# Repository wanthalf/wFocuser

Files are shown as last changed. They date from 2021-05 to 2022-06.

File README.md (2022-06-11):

# wFocuser (extension of myFocuserPRO2 ESP)

This is my private extension of the original "myFP2ESP Firmware for ESP32 and ESP8266 myFP2ESP Controllers" by Robert Brown, Holger Manz and Paul Porters, forked from the [brownrb/myFP2ESPFirmware](https://github.com/brownrb/myFP2ESPFirmware) repository. The original README.md is renamed to [README.myFP2ESP.md](README.myFP2ESP.md) and contains links to the original project information and documentation.

## Motivation and changes

MyFocuser is a marvellous project (actually a group of projects) for building DIY electronic focusers primarily aimed at astrophotography. They cover various combinations of hardware components suitable for differently sized equipment (telescopes or photolenses). However, the broad field of supported components and their features has its limits, of course. Once you get used to the peculiarities of this project and occasional inconsistencies or contradictions within the otherwise admirable, long and detailed documentation, you may want to adapt or extend the focuser to your own needs or ideas. My desire was to get beyond two basic limitations of the original project based on the ESP32 microcontroller:
1. MyFocuser is primarily aimed at *remote control*, but it already implements two pushbuttons for local quick adjustment of the focus and an OLED display for information about the focuser. I wanted to be able to use the pushbuttons to control all the main functions of the focuser *locally*, too. For that purpose I added two more pushbuttons and extended the source code of the firmware to fully utilize the possibilities of the OLED display.
2. The original documentation expects you to use one of the pre-designed PCB boards. That seems rather a complication to me (where to get it?) and it also expects you to place the focuser board into a relatively large box and use robust cable interconnections with other components (stepper motor, sensors etc.); I wanted a more compact and lightweight build suitable for travelling with my portable equipment (ExploreScientific iExos-100 mount controlled by a small Astroberry) which could ideally be fixed directly to the telescope tube.

My build is based on the ESP32 controller, SH1106 OLED 1,3" display, TMC2209 driver and a NEMA17-PG27 motor. I tried to modify the firmware with the effort of the minimal possible interventions in order to keep backward compatibility with all the originally supported hardware components and features, but I cannot guarantee I did not really break anything. I cannot test or "support" any other hardware combinations (beyond theoretical help), but I tried to avoid disrupting any of the functionality of the original firmware.

The changes concern:

- the original pushbuttons (called UP/DOWN) have their primary functionality modified so that they can move the focuser in smaller or larger (but exact) amount of steps, depending on the length of their press
- adding two more push buttons called MOD(ifier) and SET to control all functions of the focuser locally via an interactive menu; use of an OLED display is needed

## Advanced control in detail

The display can show 4 different basic screens (pages) which can be switched by a short press of the SET button:

1. MAIN page is almost identical with the original screen in OLED_GRAPHIC mode: it shows the focuser's current position, direction of movement and target position, as well as the maximal position, step size, backlash, temperature (if available), "heart beat" symbol and an additional symbol to indicate connection of remote client; only this page allows the UP/DOWN buttons to be used to move the focuser interactively\
MAIN PAGE
2. PRESET page allows to apply one of the 10 available presets or to edit/change their values\
PRESETS PAGE
3. SETTINGS page allows to change the following 10 most important settings: enable or disable home position switch, temperature probe, backlash-in and backlash-out compensation; changing the value of the current and maximal position (without moving the focuser); changing motor speed, step size, backlash-in and backlash-out amount of steps\
SETTINGS PAGE
4. NETWORK information: showing the current SSID and IP address of the WiFi connection and state of the remote client connection (ASCOM/INDI)

### Turning the display ON/OFF

The original behaviour of myFocuser is kept: when the firmware stores the changed position or settings into permanent memory, the display turns off automatically; this usually happens 30 seconds after the last movement or change of any setting. However, manual control can also be used:

- pressing any button (also just the MOD button) turns the display on
- long press of the SET button turns the display off

This behaviour is available independently of the screen/page shown.

### MAIN page

- UP/DOWN buttons can be directly used to move the focuser: a short press moves it immediately by a single step, if the button remains pressed for at least 200ms, it adds 9 more steps to reach the sum of 10, and a very long press (>900ms) adds another 90 steps to reach a full movement of 100 steps; this functionality is not dependent on the availability of a display and can be disabled by commenting out the line `#define ADVANCED_PB_MOVEMENT` in `focuserconfig.h` (then the buttons will behave as in the original firmware); at the same place in the configuration, you can also modify the press length times/thresholds for the short/bold and long press (`BOLDPRESS`, `LONGPRESS`) and the step sizes for each movement phase (`SHORT_STEPS`, `BOLD_STEPS`, `LONG_STEPS`)
- MOD + UP/DOWN: changes the numeric value of the target position shown on the display (the longer you press the buttons, the faster the numbers change); unlike the direct movements, where the UP button moves the focuser inwards (towards position 0) and the DOWN button outwards (towards maximal position), here the UP button changes the value up towards the maximal position and the DOWN button down to zero
- MOD + SET: move the focuser to the target position set by pressing MOD + UP/DOWN; a confirmation screen will appear (press UP to confirm or DOWN to cancel the movement)
- MOD + SET (long press): move the focuser to home position 0 (confirmation will be required too)

### PRESET page

- UP/DOWN: move between the 10 presets; if some preset value is already changed, a confirmation will be required to store or cancel the new value before moving to another preset
- MOD + UP/DOWN: change the value of the current preset; a changed value is indicated by the cursor changing into a rectangle (losing its inversion)
- MOD + SET: move the focuser to the currently selected preset position; confirmation will be required; if the preset value has been changed, another confirmation to store the value will be required first
- MOD + SET (long press): current focuser position will be set as the new value for the selected preset
- SET: switching to next page will cancel any change to the value of the current preset

### SETTINGS page

- UP/DOWN: move between the 10 available settings
- MOD + UP/DOWN: changes the current setting value; on/off values are changed immediately, numeric values are changed like the presets and need to be confirmed in order to be stored permanently (after moving UP/DOWN, away from the current setting)

## Hardware changes

After some experiments, I found out the 28BYJ-48 won't be capable to reliably move the focuser of my telescope. Therefore I deployed the "large and heavy" NEMA17-PG27 which also has very fine steps without the need for microstepping.

I managed to fit the whole controller (including the 4 push buttons) onto a small 40x60mm PCB breadboard as documented in detail in the [hardware](hardware/) folder. Together with the motor and the 1,3" OLED display, it fits comfortably into a box the size of 112x75x58mm. Of course, my build is not as robust and "clean" as the original projects based on a proper PCB and quality wiring.

The two additional pushbuttons (=the GPIO pins they are connected to) must be configured in the board configuration JSON file uploaded to the board. I modified only the `data/boards/57.jsn` configuration for the TM2209 drivers. If you use a different driver, you have to add the two additional GPIO pin assignments to the corresponding configuration file.

By accident, I also connected the second button (DOWN) to GPIO 25 instead of the original GPIO 35. But you can just revert that setting in `data/boards/57.jsn` and use the original pin.

## TMC2209 and StallGuard (remaining problems)

I did not manage to make the StallGuard work with the NEMA17-PG27 motor. The StallGuard alert is triggered by the TM2209 at nearly every start and stop of the motor movement (especially when several short moves follow each other), whatever value of the SG threshold I tried. For now, I have attached an infrared sensor to detect the home position, but a mechanical switch would probably be more precise. I still wonder whether accelerated driver control (such as AccelStepper or FastAccelStepper) would possibly help as suggested in some discussions about this kind of problems with TMC2209.

I also didn't find any real effect of all the TM2209 calculations and settings suggested in the documentation. The most important one of them (the CS value) is not set anywhere in the original firmware code anymore. I didn't observe any significant change when playing with the values, nor any significantly helpful effect on the false StallGuard alerts. But I am no expert in motor control, so I would be very thankful for any better explanation.

I also did not find the default microstepping of 4 helpful in combination with the PG27 gear of the motor and set it back to 1. Also the motor speed delay of at least 2000 seems more appropriate for the motor. Those are the other changes in the default TM2209 configuration in `data/boards/57.jsn`.

## Other questions I did not find an answer to in the official documentation

(Maybe just because I did not read everything thoroughly enough?)

#### What is the exact original behaviour of the pushbuttons?

As stated in the documentation, the pushbuttons are (originally) suitable for finer adjustments of the focuser, but not for significant movements. In practice, the pushbuttons move the focuser by a single step as long as they are pressed. That means: by one step each time the button is tested for press. The buttons are not tested when the focuser is moving. But single step movements are very short, so that you always get a movement of several steps at once even if you press the button just shortly. If you keep it pressed, the movements start to add in short intervals, so that you can reach a change of position of several dozens steps in reasonable time. In this way, you can realistically move the focuser by about 100 steps or even more with a bit of patience, but larger movements would just take too much time (several minutes).

#### Do I need to buy components from the suggested sellers?

Of course not. But if you want to use the pre-designed PCBs, you have to watch out that you buy an identical version with the same dimensions and pinout. The ESP32 modules are produced in various versions. They may have a different number of pins even though they look similar. Basically, the ESP32 modules with a single row of pins on each side are produced with 2x15 pins or 2x19 pins - the first one is the one you want for this project.

You need to take care especially in the case of the TMC2209 modules. The version from BigTreeTech is probably really unavoidabe, because other modules have not only a different pinout, but they may even be missing some important pins completely.

#### Do I need to use the pre-designed PCB?

No. But the whole documentations expects you to do it. The original PCB designs support all the available options and you may freely switch between them. That is not necessarily what you plan to do. However, you may change your mind when you try working with the focuser, so this gives you some flexibility. The original PCB gives you a lot of flexibility and robustness, but it also takes some space.

The whole wiring is actually not as complicated as it may seem at the first look. The most "complicated" is the power circuit. It contains a voltage regulator to reduce the 12V power to the 8V or 5V needed by the microcontroller, three or four capacitors, a diode and a fuse. All the rest are just interconnections between the ESP32 and its peripherals (with occasional pull-up or pull-down resistors): the stepper driver, OLED display, joystick or push buttons, temperature probe and IR sensor. The default wiring scheme also includes additional jumper headers to allow you to switch between the exclusive options in case you change your mind. These make the wiring seem more complex than it is.

#### What are all the options available?

It may be a bit difficult to find your way among all the options and variants of myFocuser at first. A great deal of information is spread to several places in the documentation and while there may be occasional inconsistencies or even contradictions between them, it is worth to find all the relevant places and read them. So, what do you need to read from the rich and detailed documentation and what you just may skip?

First, you need to choose the microcontroller you want to use. You can either use Arduino (Nano) or the ESP8266 or ESP32. The latter two support WiFi (or Bluetooth) and the ESP32 is much more powerful for almost the same price, so there is probably hardly any reason to use one of the simpler options today. One important and potentially very confusing fact is, that there are two different projects depending on the platform you choose. Not only they have different firmwares (of course), but they also have separate names and documentation (with a great amount of overlap, of course):

- **myFocuserPro2** or "Arduino ASCOM Focuser Pro2 DIY" is the first version based on Arduino Nano and it has its home at https://sourceforge.net/projects/arduinoascomfocuserpro2diy/

- **myFP2ESP** is the advanced version for ESP8266 and ESP32 and its home is at https://sourceforge.net/projects/myfocuserpro2-esp32/; firmware is available from https://github.com/brownrb/myFP2ESPFirmware

Next, you can choose the other options (as long as the combinations make sense or are possible):

- **stepper motor**: depending on the power needed to move your focuser and the ability to move in short (micro)steps, you have to choose a stepper motor. For light applications, you can use the small, widely available and very cheap 28BYJ-48. For more heavy focusers, you may need a stronger NEMA stepper. I have finally used the ultimate (but also quite heavy) NEMA17-PG27 with a 1:27 gear, which has the highest torque and does not need any additional microstepping thanks to its gear, which allows up to 5370 steps per revolution directly. To find out what kind of stepping you need, you should first read the **Focuser Basics** document and decide how you would connect the stepper to your focuser (i.e. directly or via a custom gear).

- **motor driver**: may depend on the motor you choose, but generally there are quite many drivers supported: DRV8825, ULN2003 (usually sold together with the 28BYJ-48 stepper), L293D/mini, L298N, TMC2225, TMC2209 and even a closed-loop driver based on a large and expensive ST6128. I chose the TM2209 as it promised the most advanced features. However, I failed to deploy to StallGuard feature with my NEMA17-PG27 stepper, which promised electronic detection of the home position of the focuser that would spare me the need to install a mechanical home position switch. If you want to use the TMC drivers, there is an additional, more detailed document called "MYFP2-TRINAMIC"; however, there is some significant overlap (with contradictions) with the main guide and it opens for more questions than it answers.

- **display**: the ESP version supports 0,96" OLED based on SSD1306 or 1,3" OLED based on SH1106; I have also noticed some mention of Nextion displays and common character LCDs 16x2 or 20x4 and a few more, but they are probably only supported by the Arduino version of the firmware

- **temperature probe**: a DS18B20 temperature sensor is supported to allow for focus compensation based on the change of the temperature of the focuser

- **local control**: you may use two push buttons or a simple joystick to adjust the focuser manually; you can also use an IR remote control for a slightly more advanced control; I have implemented here a full control of the focuser using four push buttons

-  **home position switch**: can be added to detect the home (i.e. minimal or "zero") position of the focuser; TMC2209 promises to be able to detect it electronically just by the overload of the stalled stepper (they call the feature "StallGuard")

- **LEDs**: two LEDs are supported to indicate the focuser is moving in or out

#### Should I buy a 5V or 12V version of the 28BYJ-48 stepper?

The latest version of the guide already clearly states that you should prefer the (less common) 12V version of the stepper.

#### If using the unipolar 28BYJ-48 stepper, am I limited to the ULN2003 driver?

Not really. The stepper can quite easily be modified into bipolar using a sharp knife (and the modification can also be reversed using soldering iron). Search the internet for advice. I have tested this stepper with the TMC2209 as well.

#### What is shown on the display?

There are two modes available that you can choose in the configuration before compilation of the firmware: OLED_TEXT and OLED_GRAPHIC. The first one (text mode) seems to be the older one, offering several pages showing the current state and configuration settings of the focuser. The pages are displayed periodically in a fixed interval and order, and you can select to hide some of them online via the interface. The second (GRAPHIC) mode has just a single page showing less details, but only the most important information you would really need while using the device.

My extension is using the GRAPHIC mode and adds a few more pages (switched manually) to edit the settings as described above. The main page is almost identical with the default screen of the original graphic mode (see screenshot above).

Since the display indicates the direction of the movement, I consider the LEDs unnecessary.

#### The belt length calculator...

Yes, the belt length calculator is wrong. (Or at least it was last time I checked.) It did not deduct the part of the perimeter of the wheels that the belt does not touch anymore.

Use some other belt length calculator you may find online to check before you order a belt.

####  Can I build a focuser without PCBs and soldering? Or just to test the different options before designing the final solution?

Yes. The official documentation presents one solution using the Wemos ESP32 R3 board (there are plenty of clones available) and a DRV8825/A4988 driver. But you can actually connect just any other driver to the Wemos board as well - and also any other of the components/options. The board already integrates a 12V regulator circuit so that you only connect the other peripherals directly (and possibly add the pull-up/pull-down resistors where really necessary). As indicated by the guide, the display does not really need the pull-up resistors.

#### Do I need to enable the web interface for testing from a Windows/Linux application first? I have a Mac!

No. It is true, that the web interface to control (and configure) the movement from a browser is disabled by default. But you can also enable it via another web interface which is enabled by default: the management interface available at port 6060.

#### Where can I change the GPIO pin mapping of the peripherals?

The pin mapping is not directly coded in the code of the firmware. It is stored in the JSON configuration files within the `boards` folder of the firmware `data` that you have to upload to the ESP32 before use. Each driver board has its own configuration file in this folder. TMC2209 has number 57.

After the first boot, the firmware uses this initial configuration file (depending on the driver you use) to create a custom configuration file `board_config.jsn`, where also additional settings are stored.

#### Does the focuser remember its current position when I just turn it off suddenly?

It does if you turn it off more than 30 seconds after the last movement. This is the delay when the current state of the focuser is saved. If you have a display, it is indicated by the display turning off. Otherwise, the focuser will expect to be in the last stored position.

#### Can I inspect or modify the current configuration files on the ESP?

Yes. The management interface at port 6060 allows you to list, delete and upload files stored in the ESP32. To download a file, just attach its name after the URL of the management interface (e.g. `http://myfp2eap.local:6060/board_config.jsn`).

#### How to use the OTA (Over-The-Air) updates?

I have never used OTA on ESP32 before - and it was a mistake! The OTA offers the possibility to upload a new version of the firmware without the need to connect the ESP32 by a physical USB cable to the computer. This is just great for experimenting with the firmware, especially if you have the focuser embedded in a box,  connected to everything else and mounted to the telescope. (Also: it is a VERY bad idea to power it from the 12V power source while it is also connected to the computer (e.g for debugging via the serial USB console)! The computer gets the reduced 8V back from the USB where it itself provides 5V.) I was a bit afraid of the OTA feature, but it is much simpler than I expected.

Once you enable the feature in the code (and you may set your own password) and change the ESP partitioning to support the OTA, you even get much more memory available for your firmware (because the storage for the external sketch data is reduced).

As long as the ESP (with the OTA enabled) is connected to your local wireless network, it will automagically appear in the list of available serial ports in the Arduino IDE. You can just select it and upload a new version of the firmware as if it were directly connected via a USB cable. You only have to enter the password configured in the code.

#### If I want to use the TMC2209 StallGuard, do I need to enable the home position switch?

Yes, you need to enable it in the management interface to make it work. It uses the same signal input as the home position switch. But the signal is inverted, so that you need to define `USE_STALL_GUARD` and comment out `USE_PHYSICAL_SWITCH` in the `focuserconfig.h` when compiling the firmware. If you want to use the physical switch instead of StallGuard, just connect it to the same pin (GPIO4) instead of the DIAG pin of the TMC2209 and recompile with the two definitions reversed.

#### Do I need to use the huge and ugly connectors and wiring like the Canon DB9?

Not necessarily, but it will make your device more robust. To me, the GX connectors seem more compact and robust enough, and I would choose them to connect the stepper as well, if I did not embed the controller into the same box with the stepper motor. But I am definitely no expert.

#### How about the JACK connectors?

You are explicitly discouraged to use the JACK connectors for the temperature probe. Still I did it - and also for the home position sensor. Sorry. You don't have to follow my example. The DS18B20 temperature probes are also sometimes sold with the JACK 2,5 connector. It probably also depends on the wiring of the connector pins - especially which one you use for the 5V power. But in any case: it is never a good idea to plug or unplug the JACK connectors while the device is turned on.

#### What is the correct wiring of the stepper to the driver?

In the documentation, you can find contradictory wiring hints and images. I am not really sure myself about all details, but the two separate coils (blue/red and green/black wires for my NEMA17) should be definitely connected to the two pairs of outputs of the driver (A1/A2 and B1/B2 respectively). Usually, the two pairs' pins are numbered in the opposite order at the driver's pinout. But changing the polarity of one of the two coils of the stepper only seems to have the effect of reversing the direction of its movement. So, I suppose the polarity is not important otherwise.

Let me know if I am wrong - in this or anything else! Thanks!

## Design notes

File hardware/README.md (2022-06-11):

# wFocuser hardware

I offer here the "design" of my focuser for inspiration, including the [PCB design for KiCAD](wFocuser.kicad_pcb). The whole controller is made to fit a 60x40mm prototyping perfboard. The ESP32 should be connected to a socket at the back of the PCB. The other components can fit on the front/top, but you can also mount some of them to the back if you want (e.g. some resistors). The front and back Cu lines (red and blue) are meant just to avoid crossing, but in practice you may sometimes need (or prefer) to wire them otherwise. So do the remaining dark lines indicate a third level of wiring that should cross both the first two. (I actually really used a thin wire with black isolation for them, but also for some other interconnections.) I also used 35V capacitors C1 and C4; I suppose you could just use 16V types and spare some space.

**DISCLAIMER & WARNING**
- I have no idea how to use KiCAD and how to design PCBs. I just needed to find out how to fit all the components to a small prototyping board before I actually wire it together. So I installed KiCad and played with it without reading any documentation,  tutorial or even any howto. Feel free to show me how to do it properly! ;}
- I am very unhandy - especially when cutting holes, but also when soldering. I am sorry if the pictures scare you. Just get the idea from distance and do not enlarge them more than necessary!

## Hardware changes to the original myFocuser design

- two additional buttons (MOD and SET) added to GPIO 39 and 36, incl. two additional pull-down resistors identical to R1/R2
- the second button (DOWN) is (by accident) wired to GPIO 25 instead of 35, but you can also extend the line to pin 35 if you want to keep the original assignment
- all buttons are directly soldered to the board; they can be easily controlled by a single hand (three fingers); but you can replace them with pin headers as well
- there is no J15 header to connect a joystick nor J16/J17 jumpers to enable the pushbuttons; the pushbuttons are just "enabled" by default
- there are no J9/J12 headers for IN/OUT LEDs (but they would still easily fit on the board if you desired)
- there is no J13 header for an IR sensor (but it can be easily added, I suppose)
- the C5 capacitor is not located on the board, but you can wire it to the HPSW if you connect a real mechanical switch
- the J14 and J18 headers are merged into a single HPSW header (also adding power, e.g. for an alternative infrared sensor instead of a mechanical switch)
- there is no J4 header for a 12V power LED
- the polymer fuse is integrated (no J3 header needed)
- the power ON/OFF switch is just connected directly to the power wires (no J2 header needed)

## Header pinout

#### I2C DISPLAY

(1)+3.3V; (2) GND; (3) SCL; (4) SDA

#### HPSW

(1) DIAG; (2) SIGNAL; (3) +3.3V; (4) GND

Short pins 1 and 2 with a jumper in order to use StallGuard from the TM2209 DIAG pin; or connect a mechanical home position switch (including C5) to pins 2 and 4; or an IR home position sensor module to pins 2-4.

#### 12V power input

(1) +12V; (2) GND

#### TEMP SENS

(1) signal; (2) GND; (3) +3.3V

## Pictures

Yes, to make everything even worse, I am currently using JACK connectors (see the main [README](../README.md)) for HPSW and Temp probe. I am also considering connecting both of them through a single 4-pin JACK.

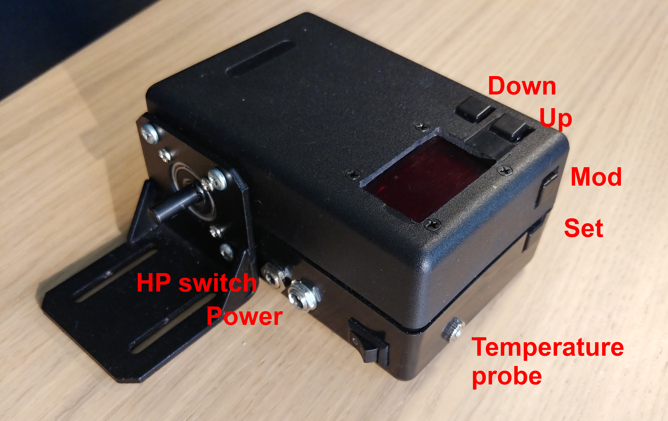
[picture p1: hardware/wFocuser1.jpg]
outside view


open box

controller detail

controller - ESP32 side

controler - TM2209 side

mounted 1

mounted 2

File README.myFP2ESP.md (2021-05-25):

# myFP2ESP Firmware for ESP32 and ESP8266 myFP2ESP Controllers
This is the firmware for the myFocuserPro2E ESP8266 and ESP32 focus controller projects on Sourceforge.

(c) Robert Brown 2019-2021
(c) Holger Manz 2020-2021 
(c) Paul Porters 2021. 
All rights reserved.

The source code is located in the **src** folder. 

#APPLICATIONS
The Windows applications are found on Sourceforge.  
https://sourceforge.net/projects/myfocuserpro2-esp32/files/Windows%20Application/  

The Linux application and source code is found on Sourceforge.  
https://sourceforge.net/projects/myfocuserpro2-esp32/files/Linux%20Application/  

The ASCOM drivers are found on Sourceforge.  
https://sourceforge.net/projects/myfocuserpro2-esp32/files/ASCOM%20Drivers/  

# FIRMWARE
The firmware is found on GitHub. Download as a zip file then extract the zip file to access the library files and firmware.  
https://github.com/brownrb/myFP2ESPFirmware/releases

# PCB GERBER FILES  
The Gerbers files for the PCB are found on Sourceforge.  
https://sourceforge.net/projects/myfocuserpro2-esp32/files/PCB%20Gerber%20Files/  

# PDF
To get a clear understanding of myFP2ESP features and options, it is essential to read the PDF.  
https://sourceforge.net/projects/myfocuserpro2-esp32/files/Documentation/  

# Compiling for ESP8266
Compiling the source code requires Arduino IDE **v1.8.13** with the ExpressIF ESP8266 Arduino extensions. You will need to add the JSON file for the ESP8266 library by using the File->Preferences menu of the Arduino IDE and add the location for the library into the board manager  
http://arduino.esp8266.com/stable/package_esp8266com_index.json  

Once specified, open the board manager, scroll down to ESP8266 and install version **v2.7.4**.
Then you can specify the target board as **Node MCU v1.0 (ESP-12E)** with Flash Size set to 4M (1MB SPIFFS) and upload speed of 115200.

Note: Additional JSON files are separated in board manager by using a comma ,

# Compiling for ESP32
Compiling the source code requires Arduino IDE **v1.8.13** with the ExpressIF ESP32 Arduino extensions.
You will need to add the JSON file for the ESP32 library by using the File->Preferences menu of the 
Arduino IDE and add the location for the library into the board manager
https://dl.espressif.com/dl/package_esp32_index.json  

Once specified, open the board manager, scroll down to ESP32 and install the latest version
Then you can specify the target board as **ESP32 Dev** with Flash Size set to 4M (1MB SPIFFS) and upload speed of 115200.

### Note1:  
Additional JSON files are separated in board manager by using a comma ,  
### Note2:  
When installed the folder C:\Program Files (x86)\Arduino\libraries\WiFi prevents compiling of ESP8266 firmware so move the WIFI folder to C:\Program Files (x86)\Arduino\libraries.old\WiFi  

# Additional JSON library Needed
Make sure you install the library ArduinoJson into the Arduino IDE else firmware will not compile.
The latest version is at https://github.com/bblanchon/ArduinoJson/releases  

# Libraries
To compile you will also need to import these libraries in the folder src/myFP2ELibs into the Arduino IDE environment using the Menu - Sketch - Include Library - Add .Zip file

* myOLED
* myHalfStepperESP32
* myDallasTemperature
* myfp2eIRremoteESP8266
* esp8266-oled-ssd1306 

Do not edit or replace any of these library files with others.

# Additional Libraries which must be downloaded and installed
To compile this firmware you need to ensure that you have installed a number of "library" files into the Arduino environment. For each of the links below, you need to DOWNLOAD the ZIP file first.

OneWire
https://github.com/PaulStoffregen/OneWire  

IRRemote
https://github.com/crankyoldgit/IRremoteESP8266  

DuckDNS
https://github.com/ayushsharma82/EasyDDNS  

ESP32 Sketch Data uploader
https://github.com/me-no-dev/arduino-esp32fs-plugin/releases/  

ESP8266 Sketch Data uploader
https://github.com/esp8266/arduino-esp8266fs-plugin 

TMC2225 requires Library TMC2208Stepper 
https://github.com/bigtreetech/BIGTREETECH-TMC2225-V1.0

TMC2209 requires library TMCStepper
https://github.com/bigtreetech/BIGTREETECH-TMC2209-V1.2

After downloading the zip files, you then need to install these into the Arduino IDE environment. To do that, start the Arduino IDE, select Sketch, Include Library, Add .Zip library, then navigate to where the ZIP files are stored and select them (you can only load 1 zip file at a time so please repeat this for all ZIP files).

The Sketch Data uploaders require a different method for installing. The install instructions are found in their respective download pages and require copying the files into a special folder of the Arduino program installation.

Once you have done this, you can start programming the controller.

# Hardware Driver Boards
One firmware file supports all driver boards [a different file supports the L293D motor shield driver board for the ESP8266]. The user must set the **DRVBRD** at the beginning of the firmware file [myBoards.h] to the correct driver board, eg,#define DRVBRD PRO2EULN2003 will set the driver board to an ULN2003 using an ESP8266 chip [myFP2Exxxx = ESP8266 and myFP2ESPxxx = ESP32].

# OLED Displays
There are two types of displays (TEXT and GRAPHICS). OLED's can also have two different Driver Chip types (SSD1306 or SSH1106) 
* OLED_TEXT requires libray myOLED
* OLED_GRAPHIC requires library esp8266-oled-ssd1306

# focuserconfig.h
Configuration information about the controller is specified in the *focuserconfig.h* file. This is where you specify the controller options like OLED_TEXT and PUSHBUTTONS, as well as the controller mode such as ACCESSPOINT or STATIONMODE.

# Controller Modes
The controller supports the modes ACCESSPOINT, STATIONMODE, LOCALSERIAL for ESP8266 with an additional BLUETOOTHMODE for the ESP32.

# Command Process Handler Routine
At present a single command process handler manages received commands for LOCALSERIAL, BLUETOOTH [ESP32 only] of TCP/IP. This must handle each controller mode, so some variables had to be made global to do this.

# FocuserSetupData.cpp and .h files
At present these must be in the same folder as the .ino file, but will later migrate to a library. These files handle the SPIFFS data, saving, restoring and persistance of controller settings. A JSON file in file system SPIFFS area is used to store focuser data.

# myBoards.cpp and .h files
This implements a driver board class for the supported driver boards [DRV8825, ULN2003, L298N, L293DMINI, L9110S]. There is one constructor for this class which accepts the boardtype, the user should never have to change the main code within the firmware file which sets up the driver boards. All pins mappings for the controller chip, hardware options and the driver board are specified here. DO NOT MODIFY THESE FILES.

# generalDefinitions.h
This file contains general definitions for all controllers, such as motor speed, step modes, focuser limits etc.

# ESPQueue.h
This file manages the Bluetooth serial data for ESP32 chips. It is a modified version of the Queue.h file from Steven de Salas. DO NOT MODIFY THIS FILE. It has been modified to work with ESP8266 and ESP32 chips.

# HalfStepperESP32 Library
This library manages the stepping modes for the ULN2003, L298N, L293DMINI and L9110S driver boards. It is a modified version of the HalfStepper library from Tom Biuso. DO NOT MODIFY THESE FILES. It has been modified to work with ESP8266 and ESP32 chips.

# myOLED Libary
This is a special cut down version of the SSD1306AsciiWire library by Bill Greiman. The library has been reduced in size and a number of additional features added. DO NOT MODIFY THESE FILES.

# COMPILE ENVIRONMENT : Tested with 
* Arduino IDE 1.8.13
* ESP8266 Core 2.7.4
* ESP32 Core 1.0.4
Libraries  
* Arduino JSON 6.18.0 https://github.com/bblanchon/ArduinoJson.git  
* myfp2eIremoteESP8266 as in Library Files
* myOLED as in Library Files
* myHalfStepperESP32 as in Library Files
* myDallas Temperature as in Library Files
* Wire [as installed with Arduino 1.8.13]
* OneWire 2.3.5 http://www.pjrc.com/teensy/td_libs_OneWire.html  
* IRRemoteESP32 as in myFP2ELibs
* EasyDDNS 1.5.9  

# Notes:  
You may need to turn 12V off to reprogram chip. Speed is 115200. Sometimes you might need to
remove the chip from PCB before re-programming new firmware. Remember to remove WIFI library
as instructed in PDF when programming ESP32.

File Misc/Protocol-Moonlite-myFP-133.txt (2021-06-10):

v1.32
18th November 2017

Moonlite uses a command sequence based on :AD# where 
    : is the beginning of the command
    AD are two alphabetic chars (A-Z) representing the command
    # is the end of command teminator

+ and - and C are exceptions and are only one character commands
numeric values in receive commands and responses are in base 16

In MOONLITE, one specifies MaxStep on the SetupDialog form of the 
ASCOM driver and the driver uses that value as a check for every 
move. MaxStep is not sent to the driver.

Standard Moonlite Protocol + myFocuserPro extensions
Command Protocol, commands begin with : and end with #
:C#     67      None    is a temperature conversion, no response
:+#     43  None        Activate temperature compensation focusing
:-#     45  None         Disable temperature compensation focusing

:GB#    16967   00#     LED backlight value, always return "00"
:GC#    17223   02#     Get the temperature coefficient, hard-coded in our example 02
:GD#    17479   xx#     Get the current step delay, only values of 02, 04, 08, 10, 20
:GH#    18503   xx#     Get if the focus motor is half-stepped (FF#) otherwise return "00#"
:GI#    18759   xx#     Get motor is moving - 01 if moving, 00 otherwise
:GN#    20039   xxxx#   Get the new motor position (target) XXXX in unsigned hex
:GP#    20551   xxxx#   Get the current motor position XXXX in unsigned hex
:GT#    21575   xxxx#   Returns the current temperature where YYYY# is a four-digit signed 
                         (2’s complement) hex number. It is multiplied by 2 by the controller
:GV#    22087   10#     firmware value, always return "10"

:FG#	18246	None	Go to the new position as set by the ":SNYYYY#" command
:FQ#	20806	None	Stop a move - like a Halt

:PH# 	18512	None	home the motor to position 0
:POXX#  20304   None    Temperature calibration offset, XX is a two-digit signed hex number, 
                         in half degree increments.
                         Example 1: :PO02# offset of +1°C, Example 2: :POFB# offset of -2.5°C

:SCXX#  17235   None    Set the new temperature coefficient where XX is a two-digit, \
                        signed (2’s complement) hex number
:SDXX#	17491	xx#	    Set the new stepping delay where XX is a two-digit, unsigned hex number. 
        			    Valid values to send are 02, 04, 08, 10 and 20, which correspond to a 
        			    stepping delay of 250, 125, 63, 32 and 16 steps per second respectively
:SF#    18003	None	Set full step mode
:SH#    18515	None	Set half step mode
:SN#    20051	None	Set new target position to nnnn (requires FG to move to target)
:SPXXXX# 20563	None	set current motor position to nnnn (does not move, updates 
        			    currentpos and targetpos to nnnn)

ENHANCEMENTS FOR myFocuser
not supported by moonlite 
Supported by myFocuser ASCOM driver
Supported by myFocuser Application
MaxStep is the maximum position of the focuser
MaxIncrement is the maximum number of steps per one move

:DG#      18244		xx#		    Get Display LCD returns state (0=disabled, 1=enabled)
:DMx#	  19780		None		Set Display in Celcius (:DM1#) or display in Fahrenheit (:DM0#)
:DS0#	  21316		None		Set Display LCD disable
:DS1#     21316		None		Set Display LCD enable

:FM#	  19782		x#		    Get Display temp mode (Celsius=1, Fahrenheit=0)

:GF#	  17991		str#		Get firmware version string#
:GM#      19783		xxxx#		Get MaxStep, returns XXXX#
:GO#      20295		xx#		    Get coils pwr setting (GO0# = coils released after move, GO1# = coil pwr on after move
:GR#      21063		xx#		    Get reverse direction setting, GRX#
:GS#	  21319		xx#		    Get stepmode (DRV8825 driver), returns XX#
:GXxxxxx#    22599				Get the time that an LCD screen is displayed for (in milliseconds, eg 2500 = 2.5seconds
:GY#      22855		xxxx#		Get MaxIncrement, returns XXXX#
:GZ#      23111		xxxxx#		Get temperature as a double GZXXXX#:

:MR#	  21069		xx#		    Get Motorspeed
:MSXX#    21325		None		Set MotorSpeed, 00 = Slow, 01 = Med, 02 = Fast
:MTxxx#	  21581		None		Set Motorspeed threshold value
:MU#	  21837		xxx#		Get Motorspeed threshold value
:MVx#     22093		None	    Set Enable/Disable motorspeed change when moving
:MW#      22349		xxx#	   	Get if motorspeedchange enabled/disabled
:MX#      22605		None  	    Save settings to EEPROM

:PG#	  18256		xx#         Get temperature precision (9-12)
:PMxx#	  19792		None		Set update of position on lcd when moving (00=disable, 01=enable)
:PN#	  20048		xx#		    Get update of position on lcd when moving (00=disable, 01=enable)
:PPxxxx#  20560		None        Set the step size value - double type, eg 2.1
:PQ#	  20816		x#		    Get if stepsize is enabled in controller (true or false, 0/1)
:PR#	  21072		xxxxx#		Get step size in microns (if enabled by controller)
:PSxx#	  21328		None		Set temperature precision (9-12 = 0.5, 0.25, 0.125, 0.0625)
:PZxx#	  23120		None		Set stepsize enabled to be OFF - default (0) or ON (1)

:SMXXXX#  19795		None		Set MaxStep between 2048 and 32000
:SOxx#    20307		None		Set coil pwr 0=release pwr after move, 1=keep power on after move
:SRxx#    21075		None		Set reverse direction setting 0=normal, 1=reverse
:SSxx#	  21331		None		Set stepmode (1=Full, 2=Half, 4=1/4, 8=1/8, 16=1/16, 32=1/32 - DRV2866 ONLY)
:SXxxxx#  22611		None		Set the length of time an LCD page is displayed for in milliseconds
:SYXXXX#  22867		None		Set MaxIncrement (anywhere between 10 and 2048)

:TA#	  16724		None		Arduino reset()

:XZ#	  23128		None		Reset the controller settings to default values

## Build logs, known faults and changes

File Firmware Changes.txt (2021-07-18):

==============================================================
myFP2ESP Focus Controller [ESP8266/ESP32]
(c) Copyright Robert Brown 2014-2021. All Rights Reserved.
(c) Copyright Holger M, 2019-2021. All Rights Reserved.
(c) Copyright Paul P, 2021. All Rights Reserved.
==============================================================

230 
// Fix for compilation errors  (focuserconfig.h)
// Clean up conditional compiler actions (focuserconfig.h)
// Fix for Preset6 not being saved correctly
// Cache presets for better interface responses  (main file and comms.h)

229
Remove INDI code[no longer needed] due to new release of myFocuserPro2 INDI driver [v10]

228
Fix for home position code on TMC2209 board

227
Add PHYSICALHPSW option to TMC2209 board as an alternative to STALLGUARD
Fix errors in checking DRV combinations which flag errors (focuserconfig.h)

226
Add moonlite protocol option
Add board PRO2ESP32ST6128 for closed loop (59.jsn)
Fix duplication of remove() in FocuserSetupData.cpp

225
Correct spelling errors
Fix I2C pin number errors in ESP8266 board config files
Fix initialization of I2C interface for most boards
Fix for OLED_TEXT initialization
Fix for OLED_GRAPHIC
Additional debug messages added
Fix for display page option (Note: Only works with OLED_TEXT)
Fix for display page time (Note: Only works with OLED_TEXT)

224
Requires Updated ArduinoJson 6-18-0 Libary - https://github.com/bblanchon/ArduinoJson
Move DefaultBoardNumber, brdfixedstepmode, brdstepsperrev into FocuserSetupData
Fix circular reference between driverboard and mySetupData when controller boots
Fix for DEBUG errors in myBoards.cpp if BOARD_DEBUG defined
Add "brdnum" to every board definition file in /data/boards
Update test programs
Fix for OLED TEXT displays - remove duplicated code in Displays.cpp

223
Fix for Infra-red remote

222-8
Add help file
Fix init of Serial.begin() 
Fix for INDI (no longer require a revision check) in comms.h

222-7
add test program (thanks Paul) to do automatic calibration of joystick values

222-6
fix for push button code - init_pushbuttons() and update_pushbuttons() as reported by Sven

222-5
Update for joystick2

222-4
Update for joystick2

222-3
Fix for Joystick2 SW routine
Add additional Joystick test programs

222-2
Move the init_homepositionswitch() code from main ino file to myBoards.cpp
Init the homeposition switch pins when driverboard constructor is called
Change code in comms.h myBoards.cpp ManagementServer.cpp to use new hpsw code in myBoards

222-1
Fix for TMC2209 hpsw detection

222
Fix for HPSW code
Fix for TMC2209 and TMC2225 initialization code
Fix for DelayAfterMove not being applied in some cases

221
Fix for TMC2209 and TMC2225 initialization

220
Fix for compilation errors on ESP8266
Add serial code support for get/set stall_value for tmc2209 [if fitted]

219
Add stall guard value to data_per.jsn
Add tmc2209current and tmc2225current to data_per.jsn
Add stall guard value to management interface get/set
Add tmc22xxcurrent set/get interface to management interface get/set
Add mutex semaphores for halt_alert, stepcount, timerSemaphore
Fix for update stepmode in webserver.cpp not obeying mySetupData->get_brdmaxstepmode()
Fix for updatestepmode in ASCOM.cpp not obeying mySetupData->get_brdmaxstepmode()
Fix for set?stallguard in ManagementServer.cpp displaying wrong text
Fix for stallguard not updating when value is changed in Management server
Fix for tmc2209current reference in myBoards.cpp
Fix for interrupt timer not disposed once move is complete
Fix for saving data files to SPIFFS - delayed if focuser is moving

218
Trinamic 2225 and 2209 support
Add stall guard support for TMC2209
Add get?commands= to show a list of get/set commands in Management Server
Fixes for comms.h to be more compatible with INDI driver
Fix for set?stepmode= in management server
Fix for set stepmode in comms.h not being set for DRVBRD == PRO2ESP32TMC2209P

217 
Fix for saveboardconfiguration

216
Move defines for STEPMODE and SPEED into boarddefs.h
Fix for stepmode not being remembered correctly or not set physically

215
[As reported/suggested by Nightfly1704]
Rename all cases of lcd to be oled for consistency
Fix setting of oled page time
Fix for saving board_config

214
Add download boardconfig.jsn to comms case 69
Add coil power timeout setting to management server (get and set) and comms cases 58 and 59
Rewrite State_Idle park routine to use coilpowertimeout rather than MotorReleaseDelay
Rewrite myBoards.h/.cpp to exclude code if those driverboards not selected
Rewrite management server set calls to return new states/values instead of generic message
Fix for get/set calls in Management Server: Incorrect usage of #ifdef ACCESSPOINT etc
Fix for ASCOM server unable to start in Management Server: State was not being set correctly
Fix for myBoards.cpp setstepmode not saving new stepmode correctly
Remove TMC chip support at this time: Software Serial Not Supported.
NEW CALLS v214
:58#		mxxxx#		Get coilpower timeout value (in millseconds)
:59xxxx#			Set coilpower timeout value (in milliseconds)
:69#		Wstring#	Get boardconfig.jsn file
//set?coilpowertimeout=30000	Set coilpower timeout release value to 30s
//get?coilpowertimeout=		Return value of Coil power timeout release (in milliseconds)
//get?boardconfig=
//get?dataconfig=

213
Add 51.jsn board file for TMC2225
Add 52.jsn board file for TMC2209
Code yet not migrated for TMC2209 and TMC2205 - do not use at this time
Ensure controller mode and options correctly applied
Fix issues with LocalSerial

212
Fix for OLEDTEXT issues and compilation errors
Change from general debug messages to targeted debug messages

211
Fixes for reboot issues
Revert to SPIFFS format - do not use LittleFS for esp8266

210
Fix for DEBUG errors

209
Fix for coil power not being released
Fix for mserver undefined in FocuserSetupData.cpp

208
Move to LittleFS on ESP8266
Rewrite /list for Management Server to work with LittleFS on ESP8266
Copy list code to FocuserSetupData.cpp 

207
Add FIXEDSTEPMODE to focuserconfig.h for boards WEMOSDRV8825H, WEMOSDRV8825, PRO2EDRV8825BIG, PRO2EDRV8825
Add STEPSPERREVOLUTION to focuserconfig.h for boards ULN2003, L298N, L293DMINI, L9110S, L293DNEMA, L293D28BYJ48
Add code to use FIXEDSTEPMODE in focuserconfig.h so value can be loaded at compile time
Add showconfig to Management Server - show current board config
Add custombrd page to Management server
Add fixedstepmode to generic get/set interface to allow user to set a fixed stepmode when using ESP8266
Create void heapmsg() to handle heap messages
Create NOTDEFINEDSTR to handle all "not defined" messages
Move INDI from focuserconfig.h to Management Server [pg3]
Improve /delete in Management server [add feedback for file not exist, file deleted and file not deleted]
Improve /upload in Management Server
Remove #ifdef around DefaultBoardNumber in myFP2ESP.ino to allow access in other files and new show board config page
Rewrite myboards.cpp stepper code based on DefaultBoardNumber rather than use strings to check for board types
Reformat [minor] Management server index page
Fix for Display not shown on / management server when oled display not defined in focuserconfig.h
Fix for Management server config page to show buttons of same width
Fix for fixedstepmode in board config not being correctly assigned

206
Add pop-up dialog box whenever reboot controller is chosen from web page on Management Server
Add preprocessor check for BLUETOOTHMODE - Halt if target is ESP8266
Initialize ipStr[] 
Fix for ipStr error when using LocalSerial mode
Fix for LocalSerial mode, to match void return of ESP_Communication() in loop()
Fix for ASCOM ALPACA REMOTE Server / page not showing all text
Increase MSpg size for MANAGEMENT Server to reserve 3700 bytes
Increase ASpg size for ASCOM Server to reserve 2200 bytes
Remove MSpg reference in ASCOM server
Remove unnecessary debug statements
Remove unnecessary [not used] defines and strings
Extract board defines into boarddefs.h and have classes include this [fixes issue of DRVBRD not being defined on some code]

205
Fix for truncated board names showing for get firmware (case 4: comms.h)
Fix for some motor board .jsn files [wrong values/pins]

204
Add references to myoled-> in ManagementServer.cpp, comms.h and webserver.cpp
Add Display_On() and Display_Off() to oled class and remove defines in management.cpp display handling code
Add Display_On() and Display_Off() stub routines in OLED_GRAPHIC class
Add checks around display methods that check displaystate - removes defines for ManagementServer.cpp and WebServer.cpp
Change code to use displaystate instead of using #if OLED_MODE or OLED_TEXT
Change all Serial.print in management.cpp/MANAGEMENT_predefinedboard1() to DebugPrint
Change web page output of MANAGEMENT_predefinedboard1() to include link to Home Page of Management Server
Rewrite case 36 in comms.h to use displaystate instead of OLED_TEXT
Rewrite WEBSERVER_handleroot() to use displaystate instead of OLED_TEXT
Rewrite OLED page info on Management Server page1 [msindex1.html]

203
Fix for ULN2003 board definition using wrong pin numbers

202
Fix for DebugPrinttt errors

201
Fix for board config not loading properly after firmware update

200
Move to board config files that are JSON descriptors of board configuration for pins etc
Add board handling routines into myFocuserData
Add web Config pages [management server] to select board config files that will reconfigure the hardware board settings
Add additional board config checks when selecting board configurations
Add additional code checks when trying to enable/disable board options in management server
Add additional code checks and new code when trying to enable/disable board options
Add new config file [board_congfig.jsn) in /data to save board hardware pin designations and board config details
Add board definition json files in /data/boards for each supported board
Add custom board definition file in /data/boards to allow a specific user defined configuration
Automatically load specified DRVBRD config file on reboot following a firmware reprogram
Delete myBoardTypes.h no longer needed
Move DRVBRD defines into focuserconfig.h
Move HOMEPOSITIONSWITCH, TEMPERATUREPROBE, INOUTLEDS, BACKLASH, PUSHBUTTONS to management server
Move list of defined board numbers to generalDefinitions.h
Rewrite myBoards.cpp to get rid of defines and use board config pins instead [found in mySetupData at runtime]
Rewrite temp.cpp routine to allow runtime loading of temperature pin from board config data
Rewrite displays.cpp to allow runtime loading of I2C data and I2C Clock pins from board config data for OLED_TEXT
Rewrite pushbutton code to allow runtime loading of pushbuttons pins from board config data
Rewrite in-outleds code to allow runtime loading of led pins from board config data
Rewrite irremote code to allow runtime loading of irremote pins from board config data
Rewrite HPS_alert code to allow runtime loading of hpsw pin from board config data
Rewrite all hpsw checks to use HPS_alert() instead of trying to read the board pin directly
Rewrite code in comms.h for handling sendpaket( float value)
Rewrite driverboard code to remove #ifdef and also no need to pass board name when instantiation of object
Rewrite init_pushbuttons() to return bool state
Rewrite init_inoutleds() to return bool state
Rewrite init_homepositionswitch() to return bool state

Path 1xx now deprecated. Path 2xx created
148
Add dummy pin defines to board configs to prevent compiler objections

147
Add WEMOSDRV8825H (Holger) to myBoards.h/.cpp and myBoardTypes.h

146
Fix for a number of compiler warnings
Fix for missing brackets in line 1141 in myFP2ESP.ino

145
Move HOMEPOSITIONSWITCH to Management Server

144
Fix for RSSI

143
Add rssi calls to comms.h and management server and webserver interfaces

142
managementserver.cpp - line 985 change to DELETE LINE Serial.print
Add stepmode up to 256 for future support of Trimac steppers
Rename temprecision to tempresolution
Disable TIMEDTESTS in generalDefinitions.h
Fix error of reboot cause by Enabling/Disabling temperature probe

141
Change driverboard->halt() - no need to return stepcount
Fix for using Serial.print commands in MachineStateBacklash - changed to DebugPrint
Fix for 2nd network credential not being updated [readwificonifg() ]
Fix for Home Position Switch not working in Backlash

140
Fix IR_HALT compile error if IRREMOTE is enabled
Fix MDNS compile errors if MDNSSERVER is enabled
Fix for Backlash
Fix for oledtextmsg compile issues when OLED_TEXT enabled
Change stepmode to int type (mySetupData and DriverBoard) to allow Trimac drivers in a future release
Add generic get/set interface calls
Add additional comms calls
Add comms calls to support myFocuserPro2 INDI driver
Add MotorSpeedDelay web page and comms calls
Allow INDI to be used over TCP/IP as well as Serial
Add additional WiFi logon credentials as a fallback
Add additional calls on webserver, temp, position, ismoving,
Fix for webserver not restarting

130
Fix for print(F()) errors
Fix for OLEDTEXT compile error
Fix for Focuser position not being updated on display when moving
Fix for HalfStepperESP32 amd mystepper library code - must reinstall
Fix for fcurrentPosition compilation errors in some options
Fix for PRO2EL293D28BYJ48 and PRO2EL293DNEMA to use myStepper library
Fix error in update_irremote() for focuser position
Fix compilation error for station mode in setup() re OLEDGRAPHICS
Fix error in ASCOM SERVER root page
Add temperature XHTML update to webserver home page wsindex.html
Add HPSW messages to generaldefinitions.h/.cpp
Completed test for all driver boards L9110S, L293D, ULN2003, L293DMINI, L298N, DRV8825

126
Rewrite web/management/ascom-remote server send page routines
Move focuserposition to driverboard.cpp, simplifies a lot of code
Implement timing statements for some code functions [to support debugging and optimization]
Implement HTTP_GET functions for most web/management/ascom server pages
Optimize web/management server code
Optimize html files and code handling routines for Webserver and Management server
Use Timer interrupts to move motor
Use common speed setting MSPEED for each driverboard
Remove speed settings in driverboard
Remove references to driverboard->setmotorspeed
Remove IRREMOTE from ESP8266 as those boards do not have support for IRREMOTE on PCB
Remove joystick speed code - now redundant 
Add ability to change temp between C/F on management web server page
Add webserver and management server page fonts/colors/layout
Add additional management web server page into 4 pages
Add management server page2 to display services to ENABLE/DISABLE WEBSERVER/ASCOMREMOTESERVER/TEMPERATUREPROBE
   and IN-OUT LEDS
Add management server page3 to display backlash settings
Add management server page4 to customize web page colors
Add management server page5 to display webpicker
Add SHOWSTARTMESSAGE to management webserver and remove define from focuserconfig.h
Add SHOWHPSWMESSAGES to management webserver and remove define from focuserconfig.h
Add MANAGEMENTFORCEDOWNLOAD to management webserver and remove define from focuserconfig.h
Add INOUTLEDS to management webserver and remove define from focuserconfig.h
Add BACKLASH to management webserver and remove define from focuserconfig.h
Add TEMPERATUREPROBE to management webserver and remove define from focuserconfig.h
Add WEBSERVER to management webserver and remove define from focuserconfig.h
Add ASCOMREMOTESERVER to management webserver and remove define from focuserconfig.h
Add SaveNow() into focuserSetupData so settings are saved immediately before rebooting
Add debug statements for printing available HEAP memory to aid debugging
Fix for motorspeed setting when using joystick or infrared remote - esp32drv8825
Fix for presets not being saved
Fix for FocuserSetupData.cpp - ESP8266 - check if file exists BEFORE attempting to delete it [avoid potential crash]
Fis for FocuserSetupData.cpp - ESP8266 - issues related to file access [avoid potential crash]
Fix for Presets on webserver presets page
Fix bug in debug statement for mdnsserver
Fix for OLED text on Management and Web server pages
Fix for display of temperature on Web Server pages
Fix for low heap memory - release web/management/ascom server strings after sending pages
Fix for low heap memory - only build strings for web/management/ascom server pages as required
Rewrite myBoards.cpp driverboard initialization code
Implement myfp2eIRemoteESP8266 library to handle IRREMOTE to reduce space footprint
Fix for focuser moving to 0 on reload
Fix for random reboots related to focusersetupdata.cpp
Fix for IRRemote key mapping for "5"
Change webserver index page to reload target position at regular intervals

122
Fix for OLED text on Management and Web server pages
Fix for display of temperature on Web Server pages
Add ability to change temp between C/F on management web server page
Presets fix
Fix for listspiffsfiles

r121
Fix issue with Home Position Switch

r120
Fix issue with tcpserver on esp8266 [port cannot be changed dynamically]
reverse direction fix (and home position switch now obeys it to)

r119
Add alpacadiscovery protocol support (UDP port 32227, IPv4)
Move ASCOMGUID into ascom definitions rather than hard coded
Fix setfeatures
Fix stepmode
On Webserver - Add ability to change TCP/IP port
Add TCP/IP port to LCD display
Fix code in management server to check for updated port numbers that change
Increase SPIFF file size for data_per.jsn

r118
Display temperature on OLED and Webserver according to tempmode state (C or F)
Add Display Enable/Disable to management console and  Web-server
Change Web-server default refresh rate to 60s [now using dynamic page update]
Reduce number of strings used in Management server and  Web-server
Add IP/DRVBRD info to Move webpage to make consistent with other web pages
Fix port number in webserver notfound page
Convert dynamic web page constants to strings into generaldefinitions.h
Add file upload to SPIFFs into management server

r117
Update copyright notice to include year 2020
When rebooting, check for MDNS and free resources
Fix code in display_oledtext_page2 to display correct port numbers for web/ascom servers
Add READWIFICONFIG as a focuser-config parameter - will read SSID and PASSWORD from wificonfig.json file
Add change port number for mDNS server to management console
Add Start and Stop mDNS server to management console
Check if service is running before attempting to stop service
Add check if MANAGEMENT server is defined without ACCESSPOINT or STATIONMODE defined
Improve layout of management console and web server pages to reduce code overhead
Move focuser presets on webpage to /presets page
Add link on main webpage to presets page
remove un-needed CRLF and spaces from data/*.html pages
Add dynamic web page update to  Web-server /move page xhttp
Add HALT to  Web-server /move page
Add focuser position and ismoving to presets webpage, add dynamic web page update xhhtp
Add ismoving dynamic update to  Web-server home page xhttp
Add halt button and move button to focuser presets web page
Add presets button to move web page
Delete move buttons from main web server page (they are on /move)
Add support for OLED 1.3" displays using SSH1106 driver chip to OLEDTEXT
Add support for OLED 1.3" displays using SSH1106 driver chip to OLEDGRAPHICS
Fix check for OLED display types and driver types
Fix issue with OLED not working on PRO2ESP32R3WEMOS board

116
Add ~finalizer for myBoards class
Fix logic error in Management server list files for ESP8266
Add DebugPrint when starting WiFi.begin()
Add DebugPrint to print error message of SPIFFS.begin() fails
Change temperature/oled update checks to use TimeCheck()
Release memory for servers ( Web-server and ascomserver) if they are stopped
Fix ESP8266 errors in defining  Web-servers and include files
Shorten some names used in SPIFFS file for data_per.jsn
Fix error in starting ascomremoteserver for ESP8266
Add reboot controller button in Management Console
Change all defined strings to uppercase and remove unused strings
Refine Debug and Trace statements in management and web server code
For OLEDTEXT, add detection for I2C display presence
For OLEDTEXT, add checks in routine for displayfound == true

115
Add duckdns mdns otaupdate etc to management page msindex.html
Fix duckdns incorrect define and checks in focuserconfig.h
Add duckdnsstate to main .ino
Rename otaserverstate to otaupdatestate
Add code in management server to handle duckdns state
Add refreshrate for webpages into management console
Add /move page to  Web-server
Add range check for focuser position and presets on  Web-server
Add range check for focuser position and maxsteps on ascom server setup
Improve speed of management and  Web-server pages
Fix issue with IRREMOTE - change to new library
Fix issue with JOYSTICK when moving and release of coil power
In State_Idle, when parking, enforce rule of releasemotor only if coilpower is false
Add TRACE macro
Increase data_per.jsn size to 1023

114
Fix LOCALSERIAL issue
Add INDI config so can work in LOCALSERIAL with INDI
Fix local serial issues line to serialline
Fix for serial.begin() ifdef LOCALSERIAL
Fix for using localserial with INDI serial driver for myFocuserPro2
Fix case 64: comms.h for check focuser position against maxstep
Fix readtemp to read_temp in graphics oled and ascom server temp routines
Change debugprint recstr in comms.h
Fix define for oledgraphics in focuserconfig.h
Implement static pages for ascom server in SPIFFS
Add code to handle new static pages in ascom server
Make small changes to header portions of all server html pages

113
Fix Bluetooth running on WEMOS ESP32
Fix LOCALSERIAL compilation errors
Move  Web-serverPORT to SPIFFS and allow MANAGEMENT SERVER to change the  Web-server port

112
Add management interface on port 6060

111
Fix temperature precision being set on boot
Move code inline
Build web pages in SPIFFS, add dynamic processor
Improve joystick code
Add calibration of joystick to pdf
Create joystick calibation and test programs in Test-programs folder

110
Add focuser presets [0-9] to use with software or infrared remote controller - stored in SPIFFS
Add options for a different joystick (2-Axis PS2 Arduino style)
Restore motorspeed before move [in case joystick has changed the speed]. 
ascomserver, comms, infraredremote, joystick,  Web-server

109
Add ASCOM REMOTE ALPACA Management interface

108
Add 2-axis joystick 
Add joystick to list of controller features

107
Allow mDNS service for most controller modes, change to port 8080

106
For revision 4 ESP32 boards, add HOME POSITION SWITCH
Add mDNS for STATIONMODE/ Web-server
For revision 4 ESP32 boards, add HOME POSITION SWITCH to PCB
Add define for HOMEPOSITIONSWITCH
Add definitions into generalDefinitions.h and myBoards.h for HPSW
Add code to handle HPSW into myFP2ESP.ino

105 04 November 2019
Add ASCOM Alpaca REMOTE support
code reduction/speed improvement in comms
separation of ascomserver, comms, display, temperature,  Web-server definitions and code into separate files

104 02 November 2019
Improve  Web-server support
 Web-server: add halt button to  Web-server
 Web-server: add setpos and gotopos buttons for position
 Web-server: fix bug for value of focuser position when updated
 Web-server: add board information and copyright
 Web-server: fix bug in motorspeed
 Web-server: add define for refresh rate of page
bracket ConnectionStatus in loop() if using ascom remote or  Web-server
add requirement to have either ACCESSPOINT or STATIONMODE defined
add requirement to have either ACCESSPOINT or STATIONMODE or BLUETOOTHMODE or LOCALSERIAL defined
implement controller features: Case 58: Get controller features
fix case 54 to return correct value for SSID when running in different modes
fix error in stepmode for PRO2ESP32DRV8825
fix setstepperspeed in DriverBoard constructor for PRO2EULN2003
fix error in oled display I2C begin, use DRVBRD == instead of defined()
improve stepper motor speed on  Web-server
fix error in case 30 as there is potential issue
oleltext: Change displaypage2 to show controller mode being used
esp_comms() now disabled if using ascom remote or  Web-server

103
Add  Web-server

102
Add PRO2ESP32R3WEMOS
Running ok on ESP32, have wired 470uf to VIN/GND and adjusted current
Add IR Mappings file
Add OTA (over the air updates)
Add LOCALSERIAL (may not work yet on all boards - does not work on L293D ESP8266 Motor Shield)
Fix display enabled bug
Remove EEPROM support, now always SPIFF
Remove motorspeedchange and motorspeedthreshold code
Add stub cases in ESP_Communication() for myFocuserPro2 support when in LOCALSERIAL mode
Extract resource strings in generalDefinitions.h file

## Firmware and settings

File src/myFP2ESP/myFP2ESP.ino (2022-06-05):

// ======================================================================
// myFP2ESP myp2esp.ino FIRMWARE OFFICIAL RELEASE 230 [18-July-2021]
// (c) Copyright Robert Brown 2014-2021. All Rights Reserved.
// (c) Copyright Holger M, 2019-2021. All Rights Reserved.
// (c) Copyright Pieter P - OTA code and SPIFFs file handling/upload based on examples
// (c) Copyright Paul P, 2021. All Rights Reserved. TMC22xx code
// ======================================================================
//
// myFP2ESP Firmware for ESP8266 and ESP32 myFocuserPro2 WiFi Controllers
// Supports Driver boards DRV8825, ULN2003, L298N, L9110S, L293DMINI, L293D, TMC2209, TMC2225
// ESP8266  OLED display, Temperature Probe
// ESP32    OLED display, Temperature Probe, Push Buttons, In/Out LED's,
//          Infrared Remote, Bluetooth
// Supports modes, ACCESSPOINT, STATIONMODE, BLUETOOTH, LOCALSERIAL, WEBSERVER,
//          ASCOMREMOTE
// Remember to change your target CPU depending on board selection
//
// ======================================================================
// SPECIAL LICENSE
// ======================================================================
// This code is released under license. If you copy or write new code based
// on the code in these files, you MUST include a link to these files AND
// you MUST include references to the authors of this code.

// ======================================================================
// CONTRIBUTIONS
// ======================================================================
// It is costly to continue development and purchase boards and components.
// Your support is needed to continue development of this project. Please
// contribute to this project, and use PayPal to send your donation to user
// rbb1brown@gmail.com (Robert Brown). All contributions are gratefully accepted.

#include "boarddefs.h"                      // include driver board and motor high level definitions
#include "generalDefinitions.h"             // include global definitions
#include "myBoards.h"                       // include driverboard class definitions
#include "focuserconfig.h"

// ======================================================================
// INCLUDES
// ======================================================================

#undef DEBUG_ESP_HTTP_SERVER                // needed sometimes to prevent serial output from WiFiServerlibrary

#include <WiFiServer.h>
#include <WiFiClient.h>
#include <ArduinoJson.h>

#if defined(ESP8266)                        // generated by Arduino IDE
#undef DEBUG_ESP_HTTP_SERVER                // prevent messages from WiFiServer 
#include <ESP8266WiFi.h>
#include <FS.h>                             // include the SPIFFS library  
#else                                       // otherwise assume ESP32
#include <WiFi.h>
#include "SPIFFS.h"
#endif
#include <SPI.h>
#include "FocuserSetupData.h"

// ======================================================================
// OVERVIEW: TO PROGRAM THE FIRMWARE
// ======================================================================
// 1. Set your DRVBRD in focuserconfig.h so the correct driver board is used
// 2. For specific boards set the FIXEDSTEPMODE in focuserconfig.h
// 3. For specific boards set the STEPSPERREVOLUTION in focuserconfig.h
// 4. Enable Display type [if fitted[ in focuserconfig.h
// 5. Set hardware options for JoyStick/IRRemote [esp32 only] in focuserconfig.h
// 6. Set the controller mode in focuserconfig.h
// 7. Set the controller protocol in focuserconfig.h
// 8. Set your target CPU to match the correct CPU for your board
// 9. Compile and upload to your controller
// 10. Upload the sketch data files

// ======================================================================
// 1: SPECIFY DRIVER BOARD in 1: focuserconfig.h
// ======================================================================
// Please specify your driver board [DRVBRD] in focuserconfig.h

// ======================================================================
// 2: SPECIFY FIXEDSTEPMODE in 2: focuserconfig.h
// ======================================================================
// For specific boards, specify the correct FIXEDSTEPMODE focuserconfig.h

// ======================================================================
// 3: SPECIFY STEPSPERREVOLUTION in 3: focuserconfig.h
// ======================================================================
// For specific boards, specify the correct STEPSPERREVOLUTION focuserconfig.h

// ======================================================================
// 4: SPECIFY DISPLAY OPTIONS IN 4: focuserconfig.h
// ======================================================================
// Specify your display options in focuserconfig.h, such as OLEDTEXT

// ======================================================================
// 5: SPECIFY HARDWARE OPTIONS IN 5: focuserconfig.h
// ======================================================================
// Specify your controller options in focuserconfig.h, such as INFRAREDREMOTE

// ======================================================================
// 6: SPECIFY THE CONTROLLER MODE IN 6: focuserconfig.h
// ======================================================================
// Please specify your controller mode in focuserconfig.h, such as
// ACCESSPOINT, STATIONMODE, LOCALSERIAL or BLUETOOTHMODE

// ======================================================================
// 7: SPECIFY CONTROLLER OPTIONS in 7: focuserconfig.h
// ======================================================================
// Please specify your controller options in focuserconfig.h, such as
// OTAUPDATES, MDNSSERVER, MANAGEMENT, USEDUCKDNS and READWIFICONFIG

// ======================================================================
// 8: SPECIFY CONTROLLER PROTOCOL in 8: focuserconfig.h
// ======================================================================
// Please specify the controller protocol in focuserconfig.h, such as
// MYFP2ESP_PROTOCOL or MOONLITE_PROTOCOL

// ======================================================================
// WIFI NETWORK CREDENTIALS: SSID AND PASSWORD
// ======================================================================
// 1. For access point mode this is the network you connect to
// 2. For station mode, change mySSID and myPASSWORD to match your network details

char mySSID[64]     = "myfp2eap";
char myPASSWORD[64] = "myfp2eap";

// Alternative network credentials if initial details above did not work
char mySSID_1[64]     = "FireFox";            // alternate network id
char myPASSWORD_1[64] = "AllYeWhoEnter";      // alternate network id


// ======================================================================
// STATIC IP ADDRESS CONFIGURATION
// ======================================================================
// must use static IP if using duckdns or as an Access Point
#ifndef STATICIPON
#define STATICIPON    1
#endif
#ifndef STATICIPOFF
#define STATICIPOFF   0
#endif
//int staticip = STATICIPON;                  // IP address specified by controller - must be defined correctly
int staticip = STATICIPOFF;                   // IP address is generated by network device and is dynamic and can change

#if (CONTROLLERMODE == ACCESSPOINT)
// By default the Access point should be 192.168.4.1 - DO NOT CHANGE
IPAddress ip(192, 168, 4, 1);                 // AP static IP - you can change these values to change the IP
IPAddress dns(192, 168, 4, 1);                // just set it to the same IP as the gateway
IPAddress gateway(192, 168, 4, 1);
IPAddress subnet(255, 255, 255, 0);
#endif // #if (CONTROLLERMODE == ACCESSPOINT)

#if (CONTROLLERMODE == STATIONMODE)
// These need to reflect your current network settings - 192.168.x.21 - change x
// This has to be within the range for dynamic ip allocation in the router
// No effect if staticip = STATICIPOFF
IPAddress ip(192, 168, 2, 21);                // station static IP - you can change these values to change the IP
IPAddress dns(192, 168, 2, 1);                // just set it to the same IP as the gateway
IPAddress gateway(192, 168, 2, 1);
IPAddress subnet(255, 255, 255, 0);
#endif // #if (CONTROLLERMODE == STATIONMODE)


// ======================================================================
// BLUETOOTH MODE NAME
// ======================================================================
#if (CONTROLLERMODE == BLUETOOTHMODE)
String BLUETOOTHNAME = "MYFP3ESP32BT";      // default name for Bluetooth controller
#endif // #ifdef BLUETOOTHMODE


// ======================================================================
// mDNS NAME: Name must be alphabetic chars only, lowercase
// ======================================================================
#ifdef MDNSSERVER
char mDNSNAME[] = "myfp2eap";               // mDNS name will be myfp2eap.local
#endif // #ifdef MDNSSERVER


// ======================================================================
// OTAUPDATES (OVER THE AIR UPDATE) SSID AND PASSWORD CONFIGURATION
// ======================================================================
// You can change the values for OTANAME and OTAPassword if required
#ifdef OTAUPDATES
#include <ArduinoOTA.h>
const char *OTAName = "ESP8266";            // the username and password for the OTA service
const char *OTAPassword = "esp8266";
#endif // #ifdef OTAUPDATES


// ======================================================================
// DUCKDNS DOMAIN AND TOKEN CONFIGURATION
// ======================================================================
// if using DuckDNS you need to set these next two parameters, duckdnsdomain
// and duckdnstoken, BUT you cannot use DuckDNS with ACCESSPOINT, BLUETOOTHMODE
// or LOCALSERIAL mode
#ifdef USEDUCKDNS
const char* duckdnsdomain = "myfp2erobert.duckdns.org";
const char* duckdnstoken = "0a0379d5-3979-44ae-b1e2-6c371a4fe9bf";
#endif // #ifdef USEDUCKDNS


// ======================================================================
// PUSH BUTTON CONTROLs
// ======================================================================

pbTimer pbUpTimer = {0, 0, 0};
pbTimer pbDnTimer = {0, 0, 0};
pbTimer pbSetTimer = {0, 0, 0};
pbTimer pbModTimer = {0, 0, 0};

// ======================================================================
// FIRMWARE CODE START - INCLUDES AND LIBRARIES
// ======================================================================

// BLUETOOTH SETTINGS - Do not change
#if (CONTROLLERMODE == BLUETOOTHMODE)
#include "BluetoothSerial.h"                  // needed for Bluetooth comms
#if !defined(CONFIG_BT_ENABLED) || !defined(CONFIG_BLUEDROID_ENABLED)
#error "Bluetooth Not enabled"
#endif
BluetoothSerial SerialBT;                     // define BT adapter to use
String btline;                                // buffer for serial data
#endif // BLUETOOTHMODE

// Project specific includes - DO NOT CHANGE
#if (CONTROLLERMODE == LOCALSERIAL || PROTOCOL == MOONLITE_PROTOCOL)
#include "ESPQueue.h"                         // by Steven de Salas
Queue queue(QUEUELENGTH);                     // receive serial queue of commands
String serialline;                            // buffer for serial data
#endif // #if defined(LOCALSERIAL)

#if ((CONTROLLERMODE == ACCESSPOINT) || (CONTROLLERMODE == STATIONMODE))
IPAddress  ESP32IPAddress;
//String     ServerLocalIP;
WiFiServer myserver(SERVERPORT);
WiFiClient myclient;                          // only one client supported, multiple connections denied
IPAddress  myIP;
#endif // #if ((CONTROLLERMODE == ACCESSPOINT) || (CONTROLLERMODE == STATIONMODE))

#include "temp.h"
TempProbe *myTempProbe;

#include "displays.h"
OLED_NON *myoled;


// ======================================================================
// GLOBAL DATA -- DO NOT CHANGE
// ======================================================================

//           reversedirection
//__________________________________
//               0   |   1
//__________________________________
//moving_out  1||  1   |   0
//moving_in   0||  0   |   1

volatile bool timerSemaphore = false;       // move completed=true, still moving or not moving = false;
volatile uint32_t stepcount;                // number of steps to go in timer interrupt service routine
volatile bool halt_alert;
#if defined(ESP8266)
// in esp8266, volatile data_type varname is all that is needed
#else
// in esp32, we should use a Mutex for access
portMUX_TYPE  timerSemaphoreMux = portMUX_INITIALIZER_UNLOCKED; // shared vars in interrupt routines must control access via mutex
portMUX_TYPE  stepcountMux = portMUX_INITIALIZER_UNLOCKED;
portMUX_TYPE  halt_alertMux = portMUX_INITIALIZER_UNLOCKED;
#endif

DriverBoard   *driverboard;
SetupData     *mySetupData;                 // focuser data

unsigned long ftargetPosition;              // target position
bool    displayfound;
byte    isMoving;                           // is the motor currently moving
char    ipStr[16] = "000.000.000.000";      // shared between BT mode and other modes

long    rssi;                               // network signal strength
int     packetsreceived;
int     packetssent;
bool    mdnsserverstate;                    // states for services, RUNNING | STOPPED
bool    webserverstate;
bool    ascomserverstate;
bool    ascomdiscoverystate;
bool    managementserverstate;
bool    tcpipserverstate;
bool    otaupdatestate;
bool    duckdnsstate;
bool    displaystate;                       // true if a display was found
bool    irremotestate;
bool    reboot;                             // flag used to indicate a reboot has occurred
int     tprobe1;                            // true if a temperature probe was detected
float   lasttemp;                           // last valid temp reading
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
void loop()
{
  static StateMachineStates MainStateMachine = State_Idle;
  static uint32_t backlash_count = 0;
  static bool     DirOfTravel = (bool) mySetupData->get_focuserdirection();
  static uint32_t TimeStampDelayAfterMove = 0;
  static uint32_t TimeStampPark = millis();
  static bool     Parked = true;                  // focuser cannot be moving as it was just started
  static bool     tms = false;                    // timersemaphore
  static uint8_t  updatecount = 0;
  static uint32_t steps = 0;

  static connection_status ConnectionStatus = disconnected;

  int stepstaken = 0;
  bool hpswstate = false;

#if defined(TIMELOOP)
  Setup_DebugPrint("loop(): ");
  Setup_DebugPrintln(millis());
#endif // #if defined(TIMELOOP)

#if ( (CONTROLLERMODE == ACCESSPOINT) || (CONTROLLERMODE == STATIONMODE) )
  if (ConnectionStatus == disconnected)
  {
    myclient = myserver.available();
    if (myclient)
    {
      if (myclient.connected())
      {
        DebugPrintln("tcp client connected");
        ConnectionStatus = connected;
        myoled->setConnectionStatus(ConnectionStatus);
        // a client has connected, start oled display again
        // oled = oled_on;
      }
    }
  }
  else
  {
    // is data available from the client request
    if (myclient.connected())
    {
      if (myclient.available())
      {
        ESP_Communication(); // Wifi communication
        // client has sent a request, turn display on
        // oled = olen_on;
      }
    }
    else
    {
      DebugPrintln("tcp client disconnectd");
      myclient.stop();
      ConnectionStatus = disconnected;
      myoled->setConnectionStatus(ConnectionStatus);
      // client has disconnected, turn display off
      myoled->display_off();
    }
  }
#endif // #if ( (CONTROLLERMODE == ACCESSPOINT) || (CONTROLLERMODE == STATIONMODE) )

#if (CONTROLLERMODE == BLUETOOTHMODE)
  if ( SerialBT.available() )
  {
    processbt();
  }
  // if there is a command from Bluetooth
  if ( queue.count() >= 1 )                 // check for serial command
  {
    ESP_Communication();
  }
#endif // ifdef Bluetoothmode

#if (CONTROLLERMODE == LOCALSERIAL)
  // if there is a command from Serial port
  if ( Serial.available() )
  {
    processserial();
  }
  if ( queue.count() >= 1 )                 // check for serial command
  {
    ESP_Communication();
  }
#endif // #if (CONTROLLERMODE == LOCALSERIAL)

#if ( (CONTROLLERMODE == ACCESSPOINT) || (CONTROLLERMODE == STATIONMODE) )
#ifdef OTAUPDATES
  if ( otaupdatestate == RUNNING )
  {
    ArduinoOTA.handle();                      // listen for OTA events
  }
#endif // ifdef OTAUPDATES
#endif // #if ( (CONTROLLERMODE == ACCESSPOINT) || (CONTROLLERMODE == STATIONMODE) )

#if ( (CONTROLLERMODE == ACCESSPOINT) || (CONTROLLERMODE == STATIONMODE) )
  if ( ascomserverstate == RUNNING)
  {
    ascomserver->handleClient();
    checkASCOMALPACADiscovery();
  }
#endif // #if ( (CONTROLLERMODE == ACCESSPOINT) || (CONTROLLERMODE == STATIONMODE) )

#if ( (CONTROLLERMODE == ACCESSPOINT) || (CONTROLLERMODE == STATIONMODE) )
  if ( webserverstate == RUNNING )
  {
    webserver->handleClient();
  }
#endif // #if ( (CONTROLLERMODE == ACCESSPOINT) || (CONTROLLERMODE == STATIONMODE) )

#if ( (CONTROLLERMODE == ACCESSPOINT) || (CONTROLLERMODE == STATIONMODE) )
#ifdef MANAGEMENT
  if ( managementserverstate == RUNNING )
  {
    mserver.handleClient();
  }
#endif
#endif // #if ( (CONTROLLERMODE == ACCESSPOINT) || (CONTROLLERMODE == STATIONMODE) )
  //_____________________________MainMachine _____________________________

  switch (MainStateMachine)
  {
    case State_Idle:
      if (driverboard->getposition() != ftargetPosition)
      {
        // we are going to move focuser, enable display
        // oled = oled_on;
        isMoving = 1;
        driverboard->enablemotor();
        MainStateMachine = State_InitMove;
        DebugPrint("go init_move");
        DebugPrint("Position:");
        DebugPrintln(driverboard->getposition());
        DebugPrint("Target:");
        DebugPrintln(ftargetPosition);
      }
      else
      {
        // focuser stationary. isMoving is 0
        if (mySetupData->SaveConfiguration(driverboard->getposition(), DirOfTravel)) // save config if needed
        {
          // we have waited 30s after move has ended so turn off display
          myoled->display_off();
          DebugPrint("Save config");
        }

        update_pushbuttons();

#ifdef JOYSTICK1
        update_joystick1();
#endif
#ifdef JOYSTICK2
        update_joystick2();
#endif
#ifdef INFRAREDREMOTE
        update_irremote();
#endif
        if (mySetupData->get_displayenabled() == 1)
        {
          myoled->update_oledtextdisplay();
        }
        else
        {
          myoled->display_off();;
        }
        myoled->Update_Oled();

        if ( mySetupData->get_temperatureprobestate() == 1)           // if probe is enabled
        {
          if ( tprobe1 != 0 )                                         // if probe was found
          {
            DebugPrintln("tprobe1 = 1");
            DebugPrintln("update_temp()");
            myTempProbe->update_temp();
          }
          else
          {
            DebugPrintln("tprobe1 = 0");
          }
        }

        // Parked is set false after State_DelayAfterMove is ended
        if (Parked == false)
        {
          if (TimeCheck(TimeStampPark, mySetupData->get_coilpower_timeout()))   // coil power off after delay time expired
          {
            // need to obey rule - can only release motor if coil power is disabled
            if ( mySetupData->get_coilpower() == 0 )
            {
              driverboard->releasemotor();
              DebugPrintln("CP=off");
            }
            Parked = true;
          } // if (TimeCheck(TimeStampPark, MotorReleaseDelay))
        } // if (Parked == false)
      } // if (driverboard->getposition() != ftargetPosition)
      break;

    case State_InitMove:
      isMoving = 1;
      backlash_count = 0;
      DirOfTravel = (ftargetPosition > driverboard->getposition()) ? moving_out : moving_in;
      driverboard->enablemotor();
      if (mySetupData->get_focuserdirection() != DirOfTravel)
      {
        mySetupData->set_focuserdirection(DirOfTravel);
        // move is in opposite direction, check for backlash enabled
        // get backlash settings
        if ( DirOfTravel == moving_in)
        {
          if (mySetupData->get_backlash_in_enabled())
          {
            backlash_count = mySetupData->get_backlashsteps_in();
          }
        }
        else
        {
          if (mySetupData->get_backlash_out_enabled())
          {
            backlash_count = mySetupData->get_backlashsteps_out();
          }
        } // if ( DirOfTravel == moving_in)
        /*
                if (DirOfTravel != moving_main && backlash_count)
                {
                  uint32_t sm = mySetupData->get_stepmode();
                  uint32_t bl = backlash_count * sm;
                  DebugPrint("bl: ");
                  DebugPrint(bl);
                  DebugPrint(" ");

                  if (DirOfTravel == moving_out)
                  {
                    backlash_count = bl + sm - ((ftargetPosition + bl) % sm); // Trip to tuning point should be a fullstep position
                  }
                  else
                  {
                    backlash_count = bl + sm + ((ftargetPosition - bl) % sm); // Trip to tuning point should be a fullstep position
                  }

                  DebugPrint("backlash_count: ");
                  DebugPrint(backlash_count);
                  DebugPrint(" ");
                } // if (DirOfTravel != moving_main && backlash_count)
                else
                {
                   DebugPrintln("false");
                }
        */
      } // if (mySetupData->get_focuserdirection() != DirOfTravel)

      // if target pos > current pos then steps = target pos - current pos
      // if target pos < current pos then steps = current pos - target pos
      steps = (ftargetPosition > driverboard->getposition()) ? ftargetPosition - driverboard->getposition() : driverboard->getposition() - ftargetPosition;
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

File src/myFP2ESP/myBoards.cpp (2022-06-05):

// ======================================================================
// myBoards.cpp : myFP2ESP DRIVER BOARD CODE
// (c) Copyright Robert Brown 2014-2021. All Rights Reserved.
// (c) Copyright Holger M, 2019-2021. All Rights Reserved.
// (c) Copyright Paul P, 2021. All Rights Reserved. TMC22xx code
// ======================================================================

// ======================================================================
// Rules
// ======================================================================
// setstepmode()
// Write
// to change a stepmode, code must call driverboard->setstepmode(smval)
// which also updates mySetupData->set_brdstepmode(smval);
// Read
// code calls mySetupData->get_brdstepmode();

// setstallguard()
// Write
// to change a stall-guard value, code must call driverboard->setstallguard(sgval)
// which also updates mySetupData->set_stallguard(smgval);
// Read
// code calls mySetupData->get_stallguard();

// settmc2209current()
// Write
// to change tmc2209 current mA value, code must call driverboard->settmc2209current(val)
// which also updates mySetupData->set_tmc2209current(val);
// Read
// code calls mySetupData->get_tmc2209current();

// settmc2225current()
// Write
// to change tmc2225 current mA value, code must call driverboard->settmc2225current(val)
// which also updates mySetupData->set_tmc2225current(val);
// Read
// code calls mySetupData->get_tmc2225current();

// ======================================================================
// Includes
// ======================================================================
#include <Arduino.h>
#include "focuserconfig.h"                // boarddefs.h included as part of focuserconfig.h"
#include "generalDefinitions.h"
#include "myBoards.h"
#include "FocuserSetupData.h"

// ======================================================================
// Externs
// ======================================================================
extern SetupData   *mySetupData;
extern DriverBoard *driverboard;

extern volatile bool timerSemaphore;
extern volatile uint32_t stepcount;                // number of steps to go in timer interrupt service routine
#if defined(ESP8266)
// in esp8266, volatile data_type varname is all that is needed
#else
// in esp32, we should use a Mutex for access
extern portMUX_TYPE timerSemaphoreMux;
extern portMUX_TYPE  stepcountMux;
#endif


// ======================================================================
// Data
// ======================================================================
bool stepdir;                                 // direction of steps to move

// ======================================================================
// timer Interrupt
// ======================================================================
#if defined(ESP8266)
#include "ESP8266TimerInterrupt.h"
ESP8266Timer myfp2Timer;                      // use a unique name for the timer
#else
#include "esp32-hal-cpu.h"                    // so we can get CPU frequency
hw_timer_t * myfp2timer = NULL;               // use a unique name for the timer
#endif

/*
  if (stepcount  && !(driverboard->hpsw_alert() && stepdir == moving_in))

  stepcount   stepdir        hpsw_alert     action
  ----------------------------------------------------
    0           x             x             stop
    >0          moving_out    x             step
    >0          moving_in     False         step
    >0          moving_in     True          stop
*/

inline void asm2uS()  __attribute__((always_inline));

// On esp8266 with 80mHz clock a nop takes 1/80000000 second, i.e. one clock pulse, or 0.0000000125 of a second
// 2 Microseconds = 2 x 10-6 Seconds or 0.000001
// To get to 2uS for ESP8266 we will need 80 nop instructions
// On esp32 with 240mHz clock a nop takes ? 1/240000000 second or 0.000000004166 of a second
// To get to 2us for ESP32 we will need 240 nop instructions

inline void asm1uS()                  // 1uS on ESP8266, 1/3uS on ESP32
{
  asm volatile (
    "nop \n\t"
    "nop \n\t"
    "nop \n\t"
    "nop \n\t"
    "nop \n\t"
    "nop \n\t"
    "nop \n\t"
    "nop \n\t"
    "nop \n\t"
    "nop \n\t"
    "nop \n\t"
    "nop \n\t"
    "nop \n\t"
    "nop \n\t"
    "nop \n\t"
    "nop \n\t"
    "nop \n\t"
    "nop \n\t"
    "nop \n\t"
    "nop \n\t"
    "nop \n\t"
    "nop \n\t"
    "nop \n\t"
    "nop \n\t"
    "nop \n\t"
    "nop \n\t"
    "nop \n\t"
    "nop \n\t"
    "nop \n\t"
    "nop \n\t"
    "nop \n\t"
    "nop \n\t"
    "nop \n\t"
    "nop \n\t"
    "nop \n\t"
    "nop \n\t"
    "nop \n\t"
    "nop \n\t"
    "nop \n\t"
    "nop \n\t"
    ::
  );
}
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

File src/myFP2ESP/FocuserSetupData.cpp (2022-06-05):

// ======================================================================
// FocuserSetupData.cpp : myFP2ESP FOCUSER DATA ROUTINES
// (c) Copyright Robert Brown 2014-2021. All Rights Reserved.
// (c) Copyright Holger M, 2019-2021. All Rights Reserved.
// ======================================================================

// ======================================================================
// Includes
// ======================================================================
#include <ArduinoJson.h>

#if defined(ESP8266)
#include "FS.h"
#else
#include "SPIFFS.h"
#endif

#include "boarddefs.h"
#include "generalDefinitions.h"
#include "FocuserSetupData.h"
#include "myBoards.h"

// ======================================================================
// Extern Data
// ======================================================================
extern byte isMoving;

// ======================================================================
// Defines
// ======================================================================
#define DEFAULTSAVETIME       30000

// ======================================================================
// SetupData Class
// ======================================================================
SetupData::SetupData(void)
{
  SetupData_DebugPrintln("Setupdata: Constructor");

  this->SnapShotMillis      = millis();
  this->BoardSnapShotMillis = millis();
  this->ReqSaveData_var     = false;
  this->ReqSaveData_per     = false;
  this->ReqSaveBoard_var    = false;

  if (!SPIFFS.begin())
  {
    SetupData_DebugPrintln("FS not mounted");
    SetupData_DebugPrintln("Formatting, please wait...");
    SPIFFS.format();
    SetupData_DebugPrintln("FS Format done");
  }
  else
  {
    SetupData_DebugPrintln("FS mounted");
    //still has issues? esp8266?
    //this->ListDir("/", 0);
  }
  this->LoadConfiguration();
};

// Loads the configuration from a file
byte SetupData::LoadConfiguration()
{
  byte retval = 0;

  // Focuser variable data - Open data_per.jsn file for reading
  File dfile = SPIFFS.open(filename_persistant, "r");
  delay(10);
  if (!dfile)
  {
    SetupData_DebugPrintln("Err: no data_per file. Create defaults.");
    LoadDefaultPersistantData();
    delay(10);
  }
  else
  {
    delay(10);
    String fdata = dfile.readString();                  // read content of the text file
    SetupData_DebugPrint("LoadConfiguration: Persistant SetupData= ");
    SetupData_DebugPrintln(fdata);                      // ... and print on serial
    dfile.close();

    // Allocate a temporary JsonDocument
    DynamicJsonDocument doc_per(DEFAULTDOCSIZE);

    // Deserialize the JSON document
    DeserializationError error = deserializeJson(doc_per, fdata);
    if (error)
    {
      SetupData_DebugPrintln("Err: no data_per file. Create defaults.");
      LoadDefaultPersistantData();
    }
    else
    {
      this->maxstep               = doc_per["maxstep"];                   // max steps
      this->stepsize              = doc_per["stepsize"];                  // the step size in microns, ie 7.2 - value * 10, so real stepsize = stepsize / 10 (maxval = 25.6)
      this->DelayAfterMove        = doc_per["delayaftermove"];            // delay after movement is finished (maxval=256)
      this->backlashsteps_in      = doc_per["backlashsteps_in"];          // number of backlash steps to apply for IN moves
      this->backlashsteps_out     = doc_per["backlashsteps_out"];         // number of backlash steps to apply for OUT moves
      this->backlash_in_enabled   = doc_per["backlash_in_enabled"];
      this->backlash_out_enabled  = doc_per["backlash_out_enabled"];
      this->tempcoefficient       = doc_per["tempcoefficient"];           // steps per degree temperature coefficient value (maxval=256)
      this->tempresolution        = doc_per["tempresolution"];            // 9 - 12
      this->coilpower             = doc_per["coilpwr"];
      this->coilpowertimeout      = doc_per["cptimeout"];
      this->reversedirection      = doc_per["rdirection"];
      this->stepsizeenabled       = doc_per["stepsizestate"];             // if 1, controller returns step size
      this->tempmode              = doc_per["tempmode"];                  // temperature display mode, Celcius=1, Fahrenheit=0
      this->oledupdateonmove      = doc_per["oledupdateonmove"];          // update position on oled when moving
      this->oledpagetime          = doc_per["oledpagetime"];
      this->tempcompenabled       = doc_per["tempcompstate"];             // indicates if temperature compensation is enabled
      this->tcdirection           = doc_per["tcdir"];
      this->displayenabled        = doc_per["displaystate"];
      for (int i = 0; i < 10; i++)
      {
        this->preset[i]           = doc_per["preset"][i];
      }
      this->webserverport         = doc_per["wsport"];
      this->ascomalpacaport       = doc_per["ascomport"];
      this->webpagerefreshrate    = doc_per["wprefreshrate"];
      this->mdnsport              = doc_per["mdnsport"];
      this->tcpipport             = doc_per["tcpipport"];
      this->startscreen           = doc_per["startscrn"];
      this->backcolor             = doc_per["bcol"].as<const char*>();
      this->textcolor             = doc_per["tcol"].as<const char*>();
      this->headercolor           = doc_per["hcol"].as<const char*>();
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

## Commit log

2021-02-24 fix for board config not being loaded after reprogram
    [FocuserSetupData.cpp, focuserconfig.h, myFP2ESP.ino]
2021-02-27 Fix for ULN2003 board definition using wrong pin numbers
    [myFP2ESP.ino]
2021-02-27 Fix for motor board definitions
    [comms.h, focuserconfig.h, myFP2ESP.ino]
2021-03-02 custom board generation
2021-03-14 Fix for mserver undefined and other issues
    [FocuserSetupData.cpp, FocuserSetupData.h, comms.h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]
2021-03-27 fixes for reboot and startup issues, remove LittleFS
    [Ascom.cpp, FORMAT-SPIFFS.ino, FocuserSetupData.cpp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]
2021-03-31 Fix for text display and ssh1106 errors
    [ManagementServer.cpp, displays.cpp, displays.h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]
2021-04-07 Update 45.jsn
    Fix error in board pins
2021-04-08 Update myFP2ESP.ino
    Fix for Bluetooth being included when bluetoothmode is not selected
    [myFP2ESP.ino]
2021-04-08 Update myBoards.cpp
    Fix for misplaced else in line 492 should have been if, not else if
    [myBoards.cpp]
2021-04-15 fix errors .ino file
    Line 342 mySetupData->set_motorSpeed(SLOW); should be -> mySetupData->set_motorspeed(SLOW);
    Line 345 mySetupData->set_motorSpeed(MED); should be -> mySetupData->set_motorspeed(MED);
    Line 348 mySetupData->set_motorspeed(FAST); should be -> mySetupData->set_motorspeed(FAST);
    Line 1253 #if (mycontrollermode == ACCESSPOINT) || (mycontrollermode == STATIONMODE) should be -> #if (CONTROLLERMODE == ACCESSPOINT) || (CONTROLLERMODE == STATIONMODE)
    as reported by Sven
    [myFP2ESP.ino]
2021-04-16 Fix page oled time, Fix boardconfig not saved
    [FocuserSetupData.cpp, FocuserSetupData.h, ManagementServer.cpp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]
2021-04-17 216. Fix for step mode not being applied to pins
    [Ascom.cpp, FocuserSetupData.cpp, ManagementServer.cpp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]
2021-04-19 fix crash when loading driverboard
    [Ascom.cpp, FocuserSetupData.cpp, ManagementServer.cpp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]
2021-04-19 fix for tmc22xx stepping and speed control
    [ManagementServer.cpp, myBoards.cpp, myBoards.h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]
2021-04-20 tmc2209 stall guard
2021-04-20 fix for hpsw code for tmc2209
    [myFP2ESP.ino]
2021-04-21 fix for set?stepmode= in management server
    [ManagementServer.cpp, focuserconfig.h, myFP2ESP.ino]
2021-04-21 add stall guard to data_per file
    [FocuserSetupData.cpp, FocuserSetupData.h, ManagementServer.cpp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]
2021-04-23 fixes for stepmode and stallguard
    [Ascom.cpp, ManagementServer.cpp, comms.h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]
2021-04-23 release interrupt timer when move complete
2021-04-23 fix for spiffs writing - now delayed if focuser is moving
    [FocuserSetupData.cpp, myFP2ESP.ino]
2021-04-24 fix for esp8266 compilation errors
    [Ascom.cpp, comms.h, generalDefinitions.h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]
2021-04-27 add serial routines for get/set STALL_VALUE
    [comms.h, myBoards.cpp, myFP2ESP.ino]
2021-05-02 fixes to hpsw and motor code
    [focuserconfig.h, generalDefinitions.h, myBoards.cpp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]
2021-05-03 fixes for stall guard and init_homepositionswitch
    [ManagementServer.cpp, comms.h, myBoards.cpp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]
2021-05-07 fix for push button code - init_pushbuttons() and update_pushbuttons() as reported by Sven
    [focuserconfig.h, myFP2ESP.ino]
2021-05-07 add test program (thanks Paul) to do automatic calibration of joystick values
2021-05-14 fix for infra-red remote
    [comms.h, focuserconfig.h, myFP2ESP.ino]
2021-05-21 move board data from myFPESP.ino into myBoards.cpp
2021-05-23 major fix for board data
    [BASIC-JOYSTICK-SW-TEST.ino, BASIC-JOYSTICK-TEST.ino, FocuserSetupData.cpp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]
2021-05-25 Fix for oled_text and test_programs update
    [FocuserSetupData.cpp, FocuserSetupData.h, INOUTLED.ino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]
2021-06-04 Add closed loop board definition for ST6128
2021-06-10 connection fix for moonlite code
    [comms.h, moonlitecomms.h]
2021-06-22 Add hompositionswitch options to TMC2209 boards
2021-06-23 Add options for HPSW using TMC2209 board
2021-08-09 Update generalDefinitions.h
    Oled config generating compilation error
    [generalDefinitions.h]
2022-06-05 Extensions for local push button & OLED control.
    Adds progressive control of movements by pushbutton press length and menu control of presets and main configuration options using 4 pushbuttons.
    Hide whitespace/linebreak to see actual changes.
2022-06-11 Add detailed documentation on all the changes from the original myFocuser.
    [wFocuser.kicad_pcb]
